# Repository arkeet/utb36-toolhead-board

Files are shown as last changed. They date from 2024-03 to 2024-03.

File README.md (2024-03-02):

# WTF is this

I wasn't satisfied with the existing toolhead boards on the market so I made
my own...

NOTE: Not tested yet

* 24V/data connection on 2x2p Micro-Fit 3.0 connector. Configured for CAN bus
  by default, but USB may be selected with solder jumpers.
* STM32G0B1 microcontroller
* Heater output on Micro-Fit 3.0 connector
* 2 thermistor ports
* 2 MOSFETs for fans, both 5V/24V selectable with solder jumpers
  * Part cooling fan output has 2 connectors in parallel
  * Hotend fan port has a sensor pin for a tachometer
* TMC2209 stepper driver
* Neopixel port
* 3 endstop ports + 1 probe port
* SPI bus exposed on 6-pin JSTSH connector (for e.g. an external
  accelerometer)

## Copyright

Copyright Adrian Keet 2024.

This source describes Open Hardware and is licensed under the CERN-OHL-S v2.

You may redistribute and modify this source and make products using it under
the terms of the CERN-OHL-S v2 (https://ohwr.org/cern_ohl_s_v2.txt).

This source is distributed WITHOUT ANY EXPRESS OR IMPLIED WARRANTY, INCLUDING
OF MERCHANTABILITY, SATISFACTORY QUALITY AND FITNESS FOR A PARTICULAR PURPOSE.
Please see the CERN-OHL-S v2 for applicable conditions.

Source location: https://github.com/arkeet/utb36-toolhead-board

As per CERN-OHL-S v2 section 4, should You produce hardware based on this
source, You must where practicable maintain the Source Location visible on the
packaging and documentation of this product or other products you make using
this source.

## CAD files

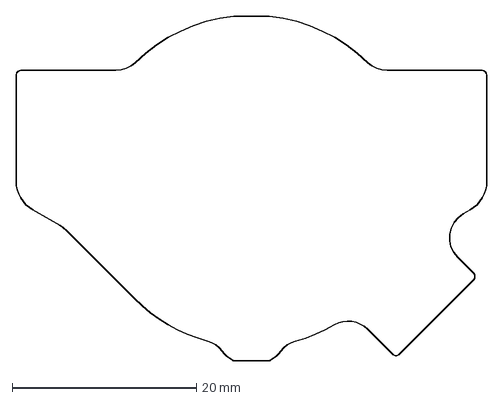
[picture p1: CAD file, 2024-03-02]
board-outline.dxf
51.0 x 37.4 mm

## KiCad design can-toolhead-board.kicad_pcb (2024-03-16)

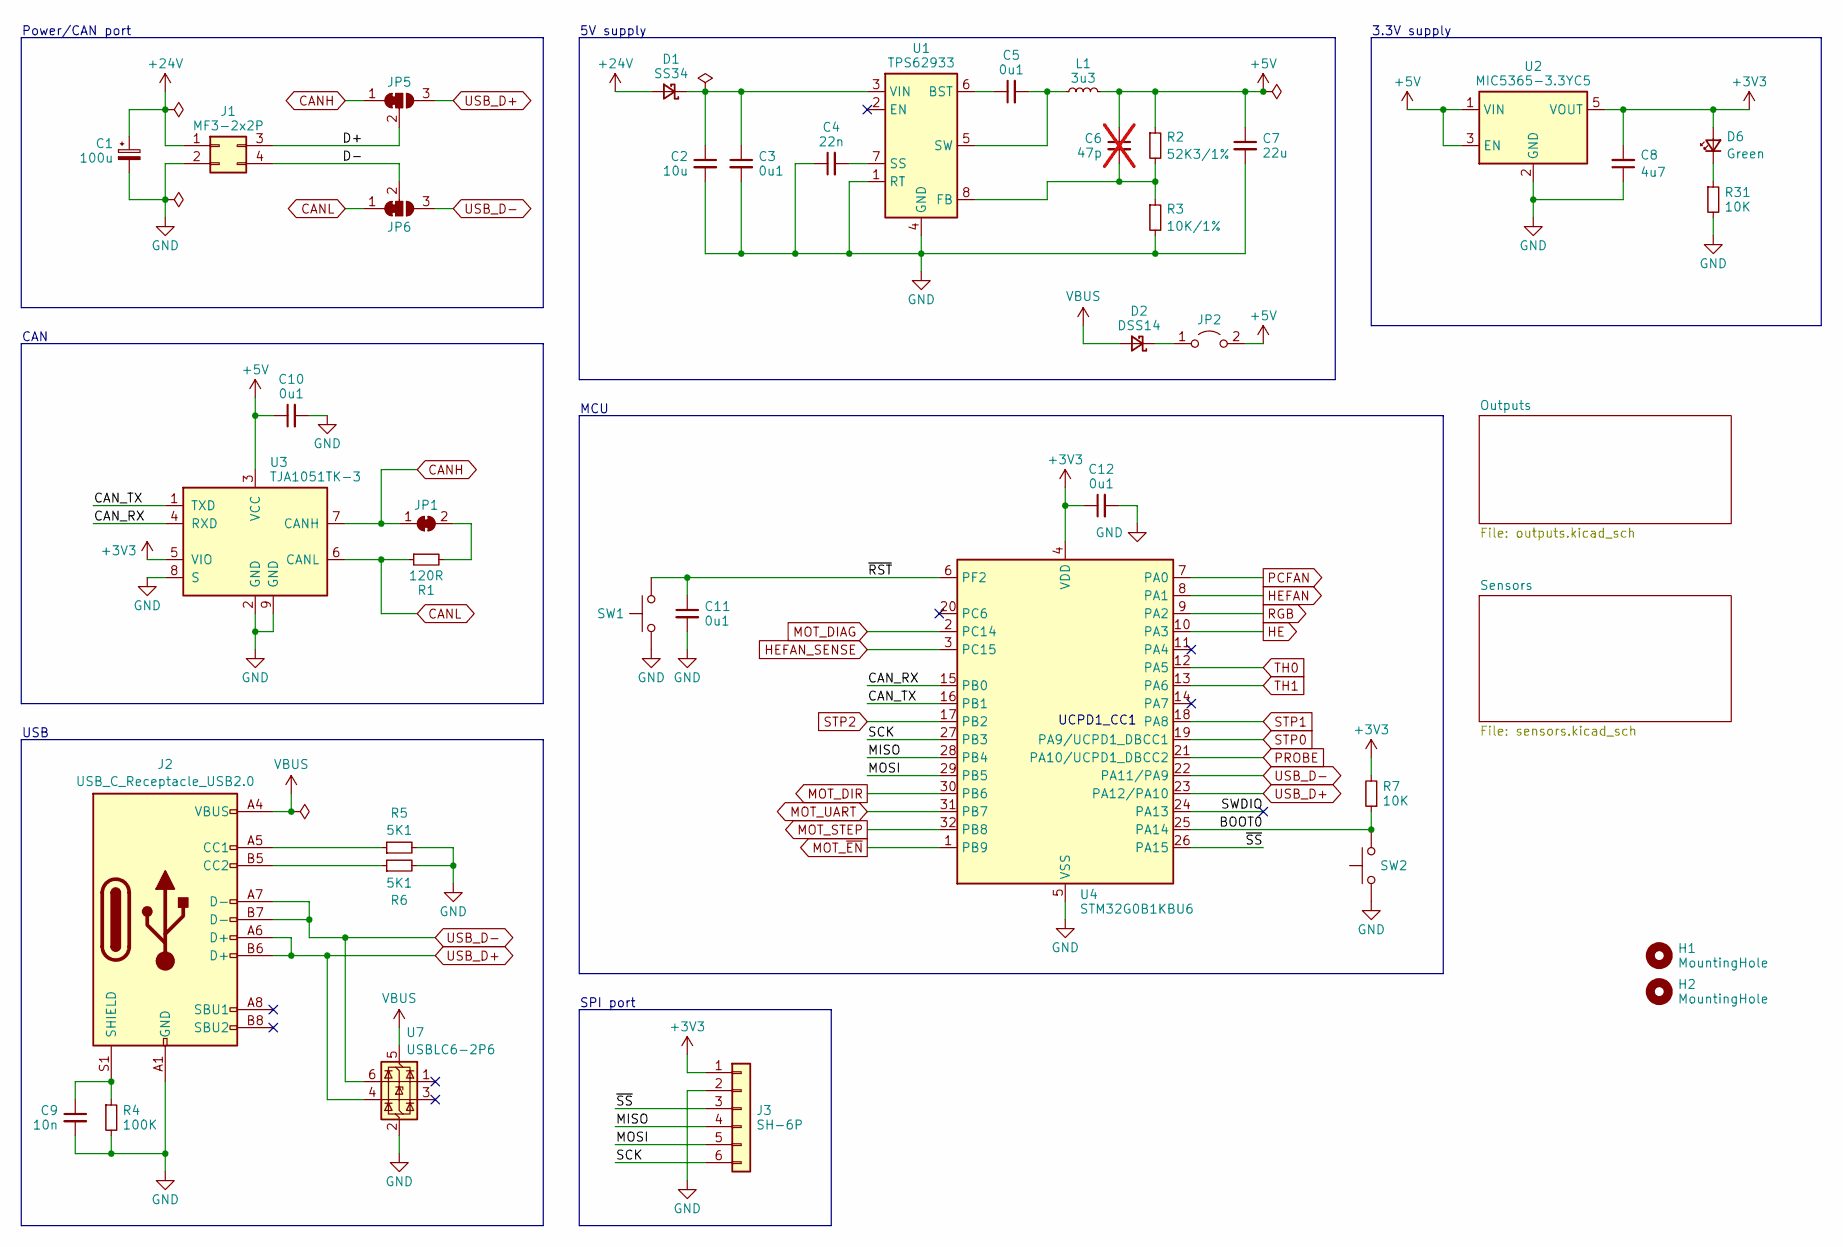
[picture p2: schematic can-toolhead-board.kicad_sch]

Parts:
C1: 100u; CP_Elec_6.3x7.7; LCSC C705528
C2: 10u; C_1206_3216Metric; LCSC C2987934
C3, C5, C10, C11, C12: 0u1; C_0402_1005Metric; LCSC C307331
C4: 22n; C_0402_1005Metric; LCSC C1532
C6: 47p; C_0402_1005Metric; LCSC C1567; not fitted
C7: 22u; C_0805_2012Metric; LCSC C258782
C8: 4u7; C_0603_1608Metric; LCSC C19666
C9: 10n; C_0402_1005Metric; LCSC C15195
D1: SS34; D_SMA; mouser# 637-SK34SMA-3G; LCSC C8678
D2: DSS14; D_SOD-123F; mouser# 241-SS1040FLR100001; LCSC C466479
D6: Green; LED_0603_1608Metric; LCSC C12624
H1, H2: MountingHole; MountingHole_3.2mm_M3_ISO7380
J1: MF3-2x2P; Molex_Micro-Fit_3.0_43045-0400_2x02_P3.00mm_Horizontal; LCSC C122413
J2: USB_C_Receptacle_USB2.0; USB_C_Receptacle_GCT_USB4105-xx-A_16P_TopMnt_Horizontal; LCSC C165948
J3: SH-6P; JST_SH_SM06B-SRSS-TB_1x06-1MP_P1.00mm_Horizontal; LCSC C160405
JP1: SolderJumper_2_Bridged; SolderJumper-2_P1.3mm_Bridged_RoundedPad1.0x1.5mm
JP2: Jumper_2_Open; PinHeader_1x02_P2.00mm_Vertical; LCSC C706997;C5274553
JP5, JP6: SolderJumper_3_Bridged12; SolderJumper-3_P1.3mm_Bridged12_RoundedPad1.0x1.5mm
L1: 3u3; L_Vishay_IHLP-2020; LCSC C845005
R1: 120R; R_0402_1005Metric; LCSC C25079
R2: 52K3/1%; R_0402_1005Metric; LCSC C276275
R3: 10K/1%; R_0402_1005Metric; LCSC C25744
R4: 100K; R_0402_1005Metric; LCSC C25741
R5, R6: 5K1; R_0402_1005Metric; LCSC C25905
R7, R31: 10K; R_0402_1005Metric; LCSC C25744
SW1, SW2: SW_Push; SW_SPST_EVQP7A; LCSC C79167
U1: TPS62933; SOT-583-8; LCSC C3200405
U2: MIC5365-3.3YC5; SOT-353_SC-70-5; LCSC C47945
U3: TJA1051TK-3; DFN-8-1EP_3x3mm_P0.65mm_EP1.55x2.4mm; LCSC C5382549
U4: STM32G0B1KBU6; QFN-32-1EP_5x5mm_P0.5mm_EP3.45x3.45mm; LCSC C5159549
U7: USBLC6-2P6; SOT-666; LCSC C2827693

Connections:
+3V3: C8.2, C12.1, D6.2 (A), J3.1, R7.2, U2.5 (VOUT), U3.5 (VIO), U4.4 (VDD); also elsewhere on the board
+5V: C6.1, C7.1, C10.1, JP2.2 (B), L1.2, R2.1, U2.1 (VIN), U2.3 (EN), U3.3 (VCC); also elsewhere on the board
+24V: C1.1, D1.2 (A), J1.1; also elsewhere on the board
/BOOT0: R7.1, SW2.2, U4.25 (PA14)
/CAN_RX: U3.4 (RXD), U4.15 (PB0)
/CAN_TX: U3.1 (TXD), U4.16 (PB1)
/D+: J1.3, JP5.2 (C)
/D-: J1.4, JP6.2 (C)
/MISO: J3.4, U4.28 (PB4)
/MOSI: J3.5, U4.29 (PB5)
/SCK: J3.6, U4.27 (PB3)
/SWDIO: U4.24 (PA13)
/~RST: C11.1, SW1.2, U4.6 (PF2)
/~SS: J3.3, U4.26 (PA15)
CANH: JP1.1 (A), JP5.1 (A), U3.7 (CANH)
CANL: JP6.1 (A), R1.1, U3.6 (CANL)
GND: C1.2, C2.2, C3.2, C4.1, C7.2, C8.1, C9.2, C10.2, C11.2, C12.2, J1.2, J2.A1 (GND), J2.A12 (GND), J2.B1 (GND), J2.B12 (GND), J3.2, R3.2, R4.2, R5.2, R6.2, R31.2, SW1.1, SW2.1, U1.1 (RT), U1.4 (GND), U2.2 (GND), U3.2 (GND), U3.8 (S), U3.9 (GND), U4.5 (VSS), U4.33 (VSS), U7.2 (GND); also elsewhere on the board
HE: U4.10 (PA3); also elsewhere on the board
HEFAN: U4.8 (PA1); also elsewhere on the board
HEFAN_SENSE: U4.3 (PC15); also elsewhere on the board
MOT_DIAG: U4.2 (PC14); also elsewhere on the board
MOT_DIR: U4.30 (PB6); also elsewhere on the board
MOT_STEP: U4.32 (PB8); also elsewhere on the board
MOT_UART: U4.31 (PB7); also elsewhere on the board
MOT_~EN: U4.1 (PB9); also elsewhere on the board
unnamed: C2.1, C3.1, D1.1 (K), U1.3 (VIN)
unnamed: D2.1 (K), JP2.1 (A)
unnamed: D6.1 (K), R31.1
unnamed: J2.A5 (CC1), R5.1
unnamed: J2.B5 (CC2), R6.1
unnamed: C9.1, J2.S1 (SHIELD), R4.1
unnamed: JP1.2 (B), R1.2
unnamed: C5.1, U1.6 (BST)
unnamed: C6.2, R2.2, R3.1, U1.8 (FB)
unnamed: C4.2, U1.7 (SS)
unnamed: C5.2, L1.1, U1.5 (SW)
PCFAN: U4.7 (PA0); also elsewhere on the board
PROBE: U4.21 (PA10/UCPD1_DBCC2); also elsewhere on the board
RGB: U4.9 (PA2); also elsewhere on the board
STP0: U4.19 (PA9/UCPD1_DBCC1); also elsewhere on the board
STP1: U4.18 (PA8); also elsewhere on the board
STP2: U4.17 (PB2); also elsewhere on the board
TH0: U4.12 (PA5); also elsewhere on the board
TH1: U4.13 (PA6); also elsewhere on the board
USB_D+: J2.A6 (D+), J2.B6 (D+), JP5.3 (B), U4.23 (PA12/PA10), U7.4 (I/O2)
USB_D-: J2.A7 (D-), J2.B7 (D-), JP6.3 (B), U4.22 (PA11/PA9), U7.6 (I/O1)
VBUS: D2.2 (A), J2.A4 (VBUS), J2.A9 (VBUS), J2.B4 (VBUS), J2.B9 (VBUS), U7.5 (VBUS)

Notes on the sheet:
UCPD1_CC1
Power/CAN port
CAN
3.3V supply
USB
SPI port
5V supply
MCU

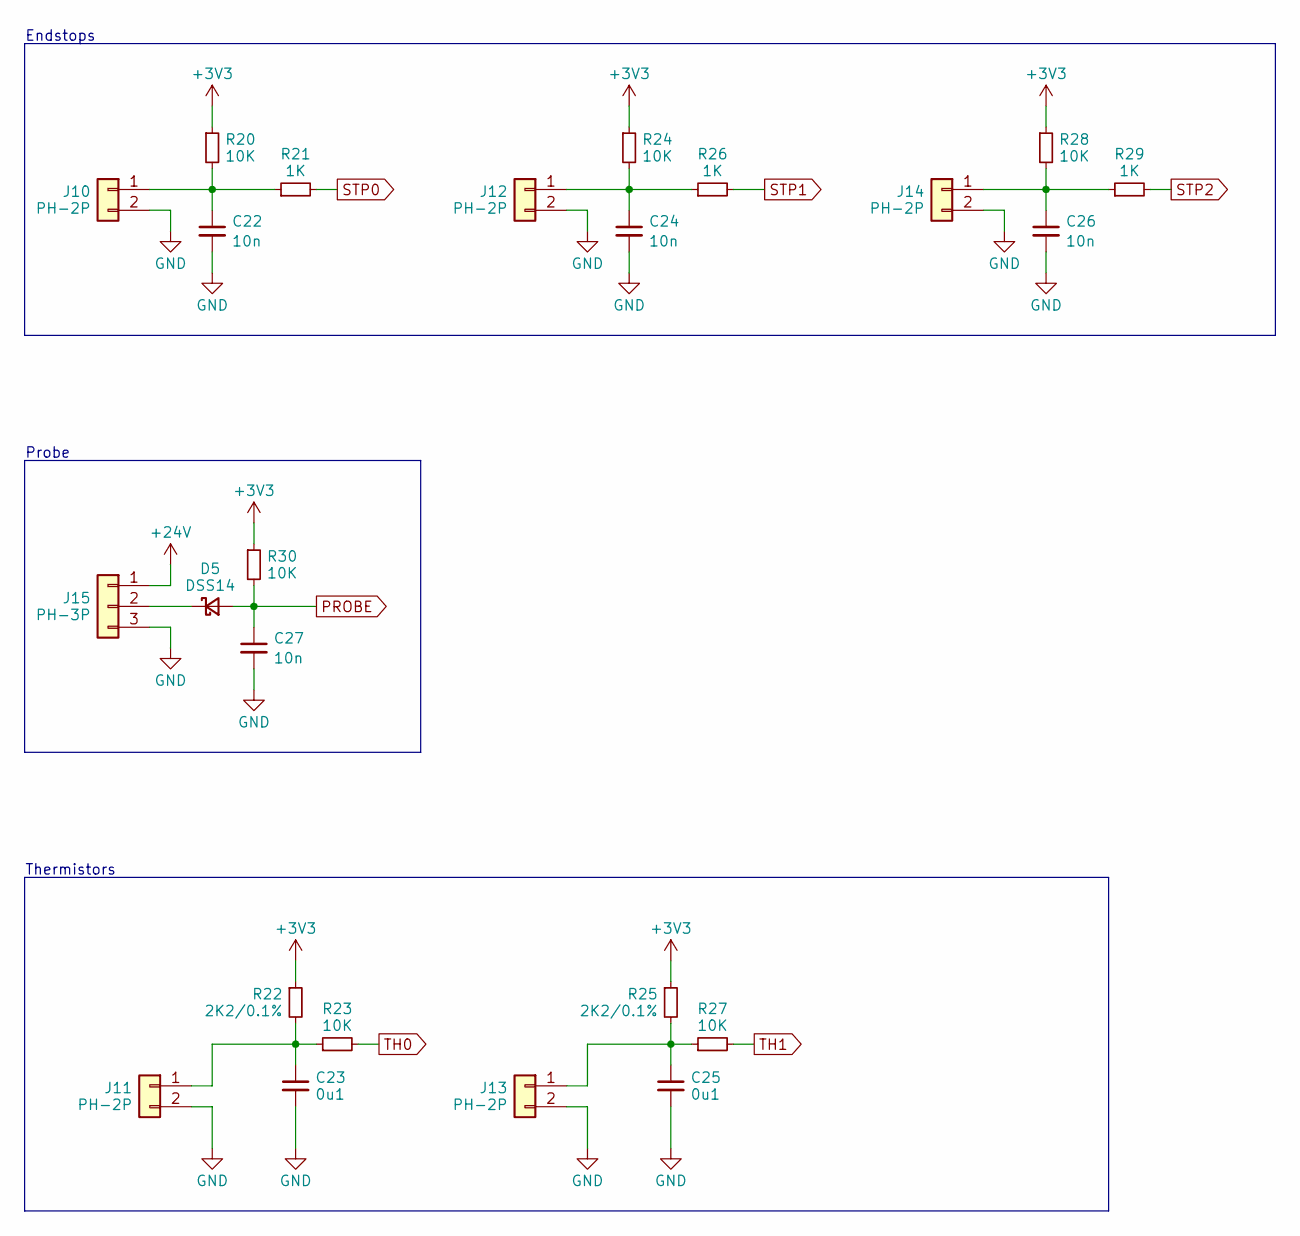
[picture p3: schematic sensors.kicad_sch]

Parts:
C22, C24, C26, C27: 10n; C_0402_1005Metric; LCSC C15195
C23, C25: 0u1; C_0402_1005Metric; LCSC C307331
D5: DSS14; D_SOD-123F; mouser# 241-SS1040FLR100001; LCSC C466479
J10, J11, J12, J13, J14: PH-2P; JST_PH_B2B-PH-K_1x02_P2.00mm_Vertical; LCSC C131337
J15: PH-3P; JST_PH_B3B-PH-K_1x03_P2.00mm_Vertical; LCSC C131339
R20, R23, R24, R27, R28, R30: 10K; R_0402_1005Metric; LCSC C25744
R21, R26, R29: 1K; R_0402_1005Metric; LCSC C11702
R22, R25: 2K2/0.1%; R_0402_1005Metric; LCSC C326602

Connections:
+3V3: R20.1, R22.1, R24.1, R25.1, R28.1, R30.1; also elsewhere on the board
+24V: J15.1; also elsewhere on the board
GND: C22.2, C23.2, C24.2, C25.2, C26.2, C27.2, J10.2, J11.2, J12.2, J13.2, J14.2, J15.3; also elsewhere on the board
unnamed: D5.1 (K), J15.2
unnamed: C22.1, J10.1, R20.2, R21.1
unnamed: C23.1, J11.1, R22.2, R23.1
unnamed: C24.1, J12.1, R24.2, R26.1
unnamed: C25.1, J13.1, R25.2, R27.1
unnamed: C26.1, J14.1, R28.2, R29.1
PROBE: C27.1, D5.2 (A), R30.2; also elsewhere on the board
STP0: R21.2; also elsewhere on the board
STP1: R26.2; also elsewhere on the board
STP2: R29.2; also elsewhere on the board
TH0: R23.2; also elsewhere on the board
TH1: R27.2; also elsewhere on the board

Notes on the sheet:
Probe
Thermistors
Endstops

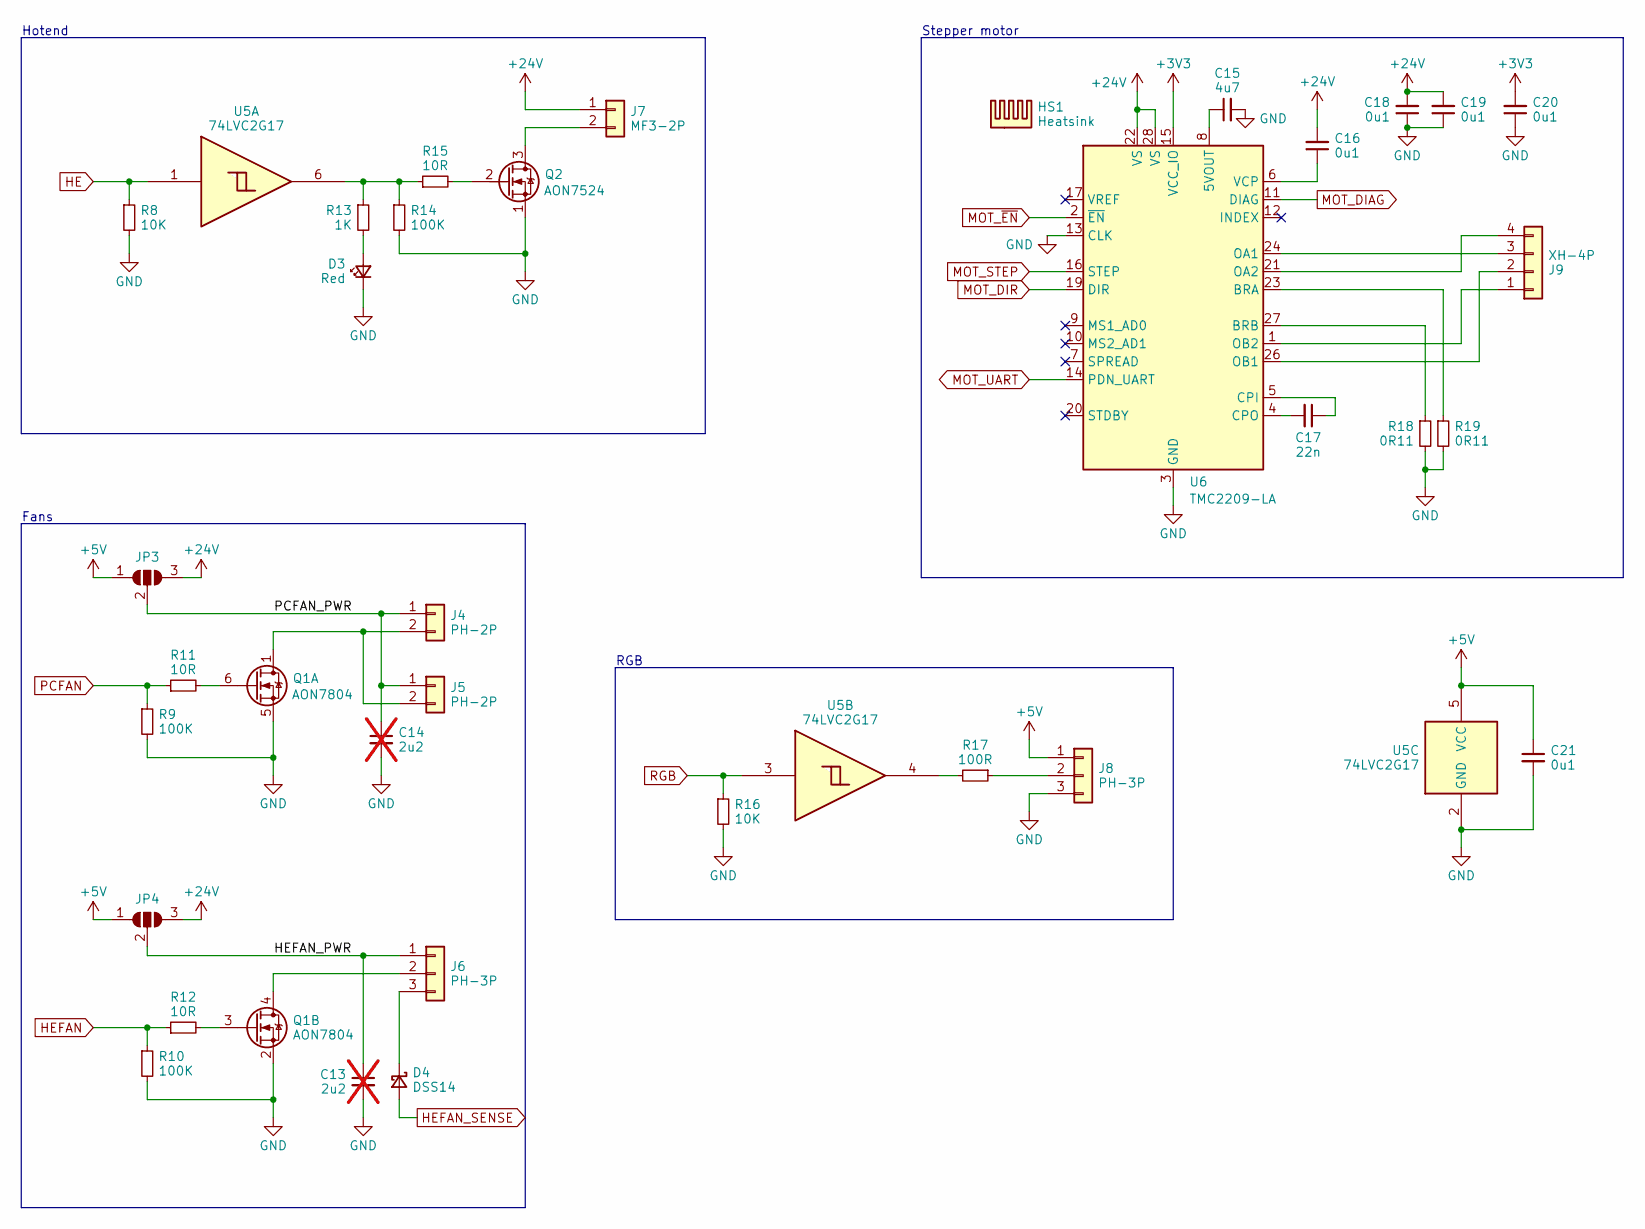
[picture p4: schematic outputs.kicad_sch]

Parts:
C13, C14: 2u2; C_0603_1608Metric; LCSC C408135; not fitted
C15: 4u7; C_0603_1608Metric; LCSC C19666
C16, C18, C19, C20, C21: 0u1; C_0402_1005Metric; LCSC C307331
C17: 22n; C_0402_1005Metric; LCSC C1532
D3: Red; LED_0603_1608Metric; LCSC C2286
D4: DSS14; D_SOD-123F; mouser# 241-SS1040FLR100001; LCSC C466479
HS1: Heatsink; Heatsink_9x9mm
J4, J5: PH-2P; JST_PH_B2B-PH-K_1x02_P2.00mm_Vertical; LCSC C131337
J6, J8: PH-3P; JST_PH_B3B-PH-K_1x03_P2.00mm_Vertical; LCSC C131339
J7: MF3-2P; Molex_Micro-Fit_3.0_43650-0200_1x02_P3.00mm_Horizontal; LCSC C192562
J9: XH-4P; JST_XH_B4B-XH-A_1x04_P2.50mm_Vertical; LCSC C144395
JP3, JP4: SolderJumper_3_Open; SolderJumper-3_P2.0mm_Open_TrianglePad1.0x1.5mm
Q1: AON7804; AO_DFN-8-2EP_3x3mm_P0.65mm_EP1.75x1mm; LCSC C431197
Q2: AON7524; AO_DFN-8-1EP_3x3mm_P0.65mm_EP1.75x2.35mm; LCSC C431195
R8, R16: 10K; R_0402_1005Metric; LCSC C25744
R9, R10, R14: 100K; R_0402_1005Metric; LCSC C25741
R11, R12, R15: 10R; R_0402_1005Metric; LCSC C25077
R13: 1K; R_0402_1005Metric; LCSC C11702
R17: 100R; R_0402_1005Metric; LCSC C25076
R18, R19: 0R11; R_0805_2012Metric; LCSC C2074624
U5: 74LVC2G17; SOT-363_SC-70-6; LCSC C7394022
U6: TMC2209-LA; QFN-28-1EP_5x5mm_P0.5mm_EP3.75x3.75mm_ThermalVias; LCSC C465949

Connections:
+3V3: C20.2, U6.15 (VCC_IO); also elsewhere on the board
+5V: C21.1, J8.1, JP3.1 (A), JP4.1 (A), U5.5 (VCC); also elsewhere on the board
+24V: C16.2, C18.2, C19.2, J7.1, JP3.3 (B), JP4.3 (B), U6.22 (VS), U6.28 (VS); also elsewhere on the board
/Outputs/HEFAN_PWR: C13.1, J6.1, JP4.2 (C)
/Outputs/PCFAN_PWR: C14.1, J4.1, J5.1, JP3.2 (C)
GND: C13.2, C14.2, C15.2, C18.1, C19.1, C20.1, C21.2, D3.1 (K), J8.3, Q1.2 (S), Q1.5 (S), Q2.1 (S), R8.2, R9.2, R10.2, R14.2, R16.2, R18.2, R19.2, U5.2 (GND), U6.3 (GND), U6.13 (CLK), U6.18 (GND), U6.29 (GND); also elsewhere on the board
HE: R8.1, U5.1; also elsewhere on the board
HEFAN: R10.1, R12.1; also elsewhere on the board
HEFAN_SENSE: D4.2 (A); also elsewhere on the board
MOT_DIAG: U6.11 (DIAG); also elsewhere on the board
MOT_DIR: U6.19 (DIR); also elsewhere on the board
MOT_STEP: U6.16 (STEP); also elsewhere on the board
MOT_UART: U6.14 (PDN_UART); also elsewhere on the board
MOT_~EN: U6.2 (~EN); also elsewhere on the board
unnamed: D3.2 (A), R13.2
unnamed: D4.1 (K), J6.3
unnamed: J4.2, J5.2, Q1.1 (D)
unnamed: J6.2, Q1.4 (D)
unnamed: J7.2, Q2.3 (D)
unnamed: J8.2, R17.1
unnamed: J9.1, U6.1 (OB2)
unnamed: J9.2, U6.26 (OB1)
unnamed: J9.3, U6.24 (OA1)
unnamed: J9.4, U6.21 (OA2)
unnamed: Q1.6 (G), R11.2
unnamed: Q1.3 (G), R12.2
unnamed: Q2.2 (G), R15.2
unnamed: R13.1, R14.1, R15.1, U5.6
unnamed: R17.2, U5.4
unnamed: C15.1, U6.8 (5VOUT)
unnamed: R19.1, U6.23 (BRA)
unnamed: R18.1, U6.27 (BRB)
unnamed: C17.1, U6.5 (CPI)
unnamed: C17.2, U6.4 (CPO)
unnamed: C16.1, U6.6 (VCP)
PCFAN: R9.1, R11.1; also elsewhere on the board
RGB: R16.1, U5.3; also elsewhere on the board

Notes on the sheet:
Fans
Stepper motor
Hotend
RGB

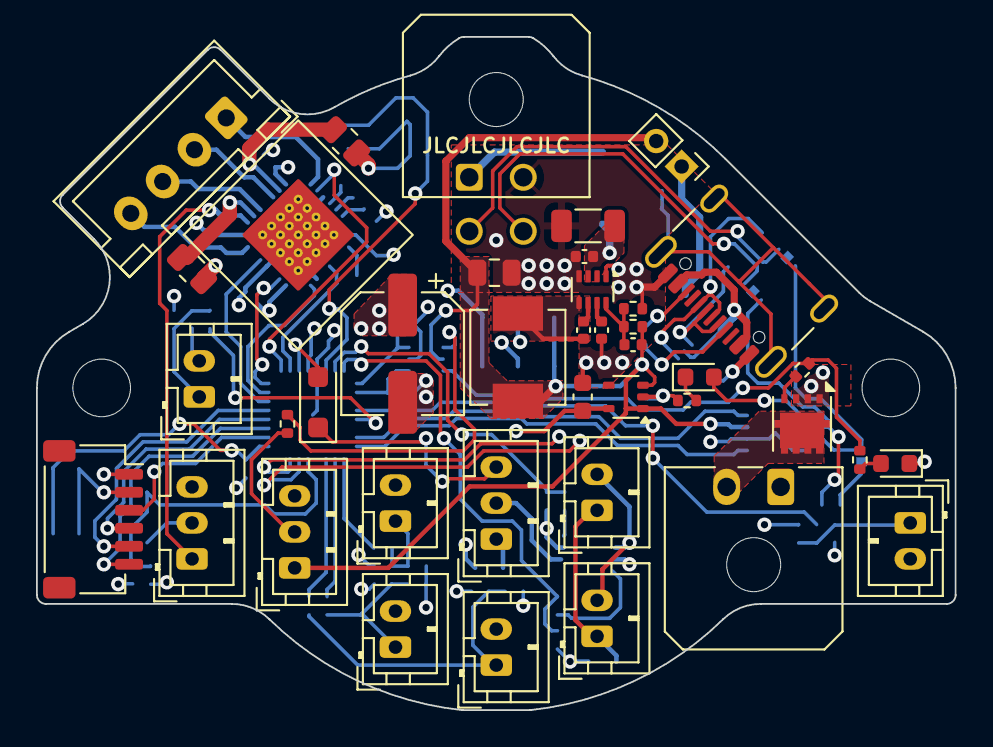
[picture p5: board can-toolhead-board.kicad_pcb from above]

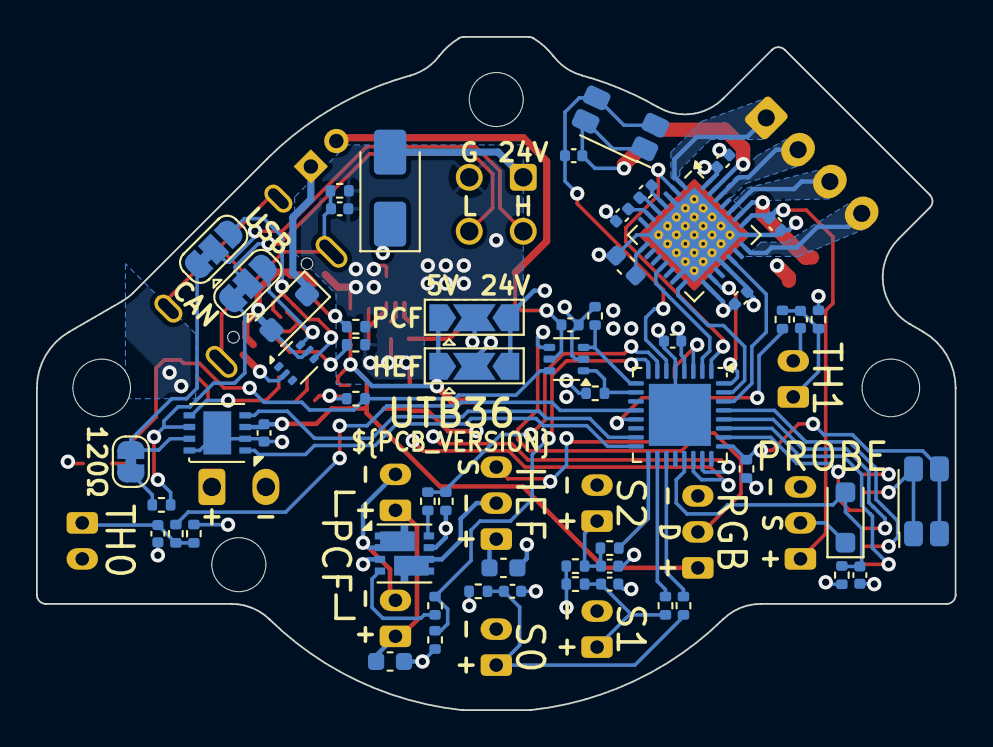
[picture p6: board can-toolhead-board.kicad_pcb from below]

Board: 4 copper layers, 51.0 x 37.4 mm, 100 parts (58 on the bottom side), 75 nets.

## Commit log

2024-02-26 Added solder jumpers for CAN/USB interface selection
    [can-toolhead-board.kicad_pcb, can-toolhead-board.kicad_sch, mcu.kicad_sch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]
2024-02-26 Layout tweaks/pinout optimization
    [can-toolhead-board.kicad_pcb, mcu.kicad_sch]
2024-02-26 Change 3V3 output cap to 4u7
    [can-toolhead-board.kicad_pcb, can-toolhead-board.kicad_sch]
2024-02-26 Rename fan ports to PCF/HEF
    Remove USB series resistors
    Add USB clamping diodes
    [can-toolhead-board.kicad_pcb, mcu.kicad_sch, outputs.kicad_sch]
2024-02-26 Add USB CC pulldown resistors
    [can-toolhead-board.kicad_pcb, can-toolhead-board.kicad_sch, mcu.kicad_sch]
2024-02-27 Add 3D models
    [can-toolhead-board.kicad_pcb, can-toolhead-board.kicad_sch, outputs.kicad_sch]
2024-02-28 Fix part LCSC ref
    [can-toolhead-board.kicad_pcb, can-toolhead-board.kicad_sch]
2024-02-28 Change 10uF cap on 24V input to 0805; change 33nF to 22nF to simplify BOM; add green power LED
    [can-toolhead-board.kicad_pcb, can-toolhead-board.kicad_sch]
2024-02-28 Lots of little tweaks and simplifications
    [can-toolhead-board.kicad_pcb, can-toolhead-board.kicad_sch, outputs.kicad_sch]
2024-02-28 Modify SPI connector pinout
    [can-toolhead-board.kicad_pcb, can-toolhead-board.kicad_sch]
2024-02-28 Add dimensions
    [can-toolhead-board.kicad_pcb]
2024-02-28 Fixed up QFN pad routing and bypass cap vias
    [can-toolhead-board.kicad_pcb]
2024-02-29 Add part number references
    [can-toolhead-board.kicad_sch, outputs.kicad_sch, sensors.kicad_sch]
2024-03-01 Change input caps
    - 100uF to electrolytic
    - 10uF to 1206/50V
    - Also fix LED on BOM to not be right angle lol
    [can-toolhead-board.kicad_pcb, can-toolhead-board.kicad_sch, outputs.kicad_sch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]
2024-03-02 Change 5V out cap to 0805
    - Shifted power/CAN connector a bit to make room, and added a bit of
    meat to the board around the mounting hole
    [board-outline.dxf, can-toolhead-board.kicad_pcb, can-toolhead-board.kicad_sch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]
2024-03-02 Update LCSC part numbers
    [can-toolhead-board.kicad_sch, outputs.kicad_sch]
2024-03-02 Remove DNP from stuff where it doesn't belong in the schematic. Also DNP the fan port caps (the BOM ones weren't rated good for 24V anyway), but in any case since I couldn't find 4.7uF/35V/0603 good 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
    Also added note for higher temp STM32, so I think all the components
    should be good to 105C, except for the JST connectors...
    [can-toolhead-board.kicad_pcb, can-toolhead-board.kicad_sch, outputs.kicad_sch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]
2024-03-16 Fix LCSC part for 74LVC2G17 (wrong package). List alternate parts in notes fields.
    [can-toolhead-board.kicad_pcb, can-toolhead-board.kicad_sch, outputs.kicad_sch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]
